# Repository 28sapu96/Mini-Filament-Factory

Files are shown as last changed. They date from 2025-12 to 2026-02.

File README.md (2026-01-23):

# Mini-Filament-Factory

-A DIY Machine to produce 1.75mm filament from plastic pellets

3D printing is cheap nowadays, with the average 1kg PLA spool costing $10-20. But, can we make it even cheaper? The answer is yes, and that is what this project aims to achieve. This is a machine that can take in cheap plastic pellets, with PLA pellets costing $2-3 per kg, and output usable 3D printer filament.  

# Project Goals
1. Filament should be acceptable by a 3D Printer, and it should print well
2. Should be easy to build and run
3. Filament should be cheap to make
4. Handles multiple types of plastic
5. Resistant to jamming and other mechanical flaws

# How Does This Work?

  To make 3D printer filament from plastic pellets, it first needs to be melted and extruded. This is the first phase. A Nema 17 stepper motor in the back drives a planetary gearbox with a 1:10 ratio. So, for every 10 rotations of the stepper motor, the output of the gearbox rotates once. Under ideal conditions, this increases the torque by 10 fold and decreases the speed by the same ratio, but in real life, friction and backlash, especially in 3D printed gears, causes energy losses which reduces the efficiency (power in vs power out). The output shaft of the gearbox then drives an auger 25mm in diameter and 430mm long (Although, the AliExpress listing doesn't tell us how long the twisty bit is, which means we can't buy a pipe of exact size). The auger rotates inside of a steel pipe which is also 25mm in inner diameter with some slight clearance. I considered using Aluminum for the pipe since it was cheaper, but the auger is made of HSS (High Speed Steel) which is much, much harder than Aluminum, so it will erode the Aluminum pipe and increase the gap between the auger and the pipe wall, which will create a gap for the molten plastic to flow back, which would be catastrophic. Steel also has a lot lower heat conductivity than aluminum, which might seem worse (since you need to heat up plastic), but it is better, since we don't want the heat from the end creeping up to the back where the hopper for plastic pellets is (it would make the plastic pellets stick early). Heat creep is also why there are fans between the end and the start of the pipe, to stop heat coming to the back of the pipe. The rotating auger pushes the pellets forward to the end of the pipe, where two 150W band heaters act as a hot end. The plastic exits through a nozzle (which is just a hole) that is ~1.75mm in diameter. The plastic then air cools, with fans assisting the process. 


  The filament doesn't come out with the diameter we need due to various factors such as die swell (molten plastic expands as it comes out of the hole), so we need to do some quality control. This is the second phase. The cooled filament strand goes into a diameter sensor. The filament passes through two roller bearings, one on the top and the other on the bottom. The one on the bottom is fixed, but the top one moves up and down with the filament diameter. The top bearing moves a lever arm, which amplifies the error by 7x. For example, if the filament is .1mm thicker than needed, the top bearing moves up .1mm, which moves the lever arm, which amplifies the distance, moving the neodymium magnet at the bottom by .7mm. The hall effect sensor picks up the motion of the magnet, and the arduino does some calculations to figure out the current filament diameter. 
  

  After the filament passes through the diameter sensor, it goes to the final phase, which is a puller. The puller also has two rollers, but only one is a bearing. The top one is a bearing that can be moved up or down by turning a small gear, which turns a larger gear with a 1:5 ratio, which turns a nut, which interfaces with a bolt at the top, moving it up or down. The bolt has a thread of 13 TPI (threads per inches), so for every 13 turns, the nut & bearing will move an inch. Spinning the small gear 5 times will turn the big gear 1 time. Spinning the big gear 1 time will move the nut by 1/13 inches, so spinning the small gear 1 time will move the nut by (1/13)/5 or 1/65 inches. The bottom roller is attached to a Nema 17 Pancake, which has just enough torque to pull the strand. The arduino controls the speed at which it pulls using the feedback from the diameter sensor. Faster pulling will thin out the filament, while slower pulling will thicken it. This process will ensure that we get accurate 1.75mm filament that can be accepted by a 3D printer.


# Full Wiring Diagram:

Mini Filament Factory

# CAD Images

Onshape Document: 
https://cad.onshape.com/documents/9f9f463344dcee8ce322f606/w/9856d2d31367ce1528b75580/e/936c6a3dbc2fb8e8e5b443f2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






# Bill of Materials
| Name | Description | Link | Quantity | Unit Price | Total Price | Running Total |
|---|---|---|---|---|---|---|
| LUJINXUN 30mmIDx50mmL\ | Band Heater | https://www.aliexpress.us/item/3256808522427468.html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 | 1 | $16.09 | $16.09 | $16.09 |
| 460mm x 25mm HSS Drill Bit | Auger Bit | https://www.aliexpress.com/item/3256809045870858.html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 | 1 | $13.29 | $13.29 | $29.38 |
| 304 Stainless Steel pipe 500mm 28ODx25ID | Steel Pipe | https://www.aliexpress.com/item/3256804686578512.html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 | 1 | $11.38 | $11.38 | $40.76 |
| MAX6675 | K Thermocouple + Amplifier  | https://www.aliexpress.com/ssr/300000512/BundleDeals2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 | 1 | $3.14 | $3.14 | $43.90 |
| Nema 17 Pancake | Stepper Motor | https://www.aliexpress.com/item/3256803688622110.html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 | 1 | $5.41 | $5.41 | $49.31 |
| 9025 12V Cooling Fan | Cooling Fan | https://www.aliexpress.com/item/3256806120222119.html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 | 4 | $3.82 | $15.28 | $64.59 |
| A4988 | Stepper Motor Driver | https://www.aliexpress.com/ssr/300000512/BundleDeals2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 | 2 | $2.71 | $5.42 | $70.01 |
| Refrigator Neodymium Magnets | 20x1mm Magnet | https://www.aliexpress.com/item/3256809781217883.html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 | 1 | $2.63 | $2.63 | $72.64 |
| SS49E | Hall Effect Sensor | https://www.aliexpress.com/item/3256808273062702.html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 | 1 | $1.59 | $1.59 | $74.23 |
| Deep Groove Ball Bearing | 15ODx6IDx5Wmm Bearing | https://jlcmc.com/product/b/C15/BR8364/deep-groove-ball-bearing-double-side-with-dust-cover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 | 4 | $0.12 | $0.47 | $74.70 |
| Deep Groove Ball Bearing Open Type | 28ODx15IDx7Wmm Bearing | https://jlcmc.com/product/b/C15/BR8362/deep-groove-ball-bearing-open-type?k=6902&productModelNumber=6902 | 4 | $0.26 | $1.06 | $75.75 |
| Hex Nut | 1/2""-13 | https://www.menards.com/main/hardware/fasteners-connectors/nuts/hex-jam-nuts/grip-fast-reg-hot-dipped-galvanized-grade-2-coarse-thread-hex-nuts/2325631/p-14444215289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 | 1 | $2.19 | $2.19 | $77.94 |
| Bolt | 1/2""-13 4-1/2"" | https://www.menards.com/main/hardware/fasteners-connectors/bolts/cap-screws-hex-bolts/grip-fast-reg-1-2-13-x-4-1-2-grade-2-galvanized-steel-hex-bolt-2-count/g2ls1241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 | 1 | $3.99 | $3.99 | $81.93 |
| Arduino Uno R3 | Microcontroller | https://www.aliexpress.us/item/3256806985353444.html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 | 1 | $5.12 | $5.12 | $87.05 |
| Solid State Relay | 3-32VDC - 24-380VAC 10A SSR | https://www.aliexpress.com/item/3256806596104544.html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 | 1 | $4.21 | $4.21 | $91.26 |
| Deep Groove Ball Bearing | 47ODx25IDx12Wmm Bearing | https://jlcmc.com/product/b/C15/BR8362/deep-groove-ball-bearing-open-type?k=6005&productModelNumber=6005 | 1 | $0.46 | $0.46 | $91.72 |
| Deep Groove Ball Bearing | 24ODx9IDx7Wmm Bearing | https://jlcmc.com/product/b/C15/BR8364/deep-groove-ball-bearing-double-side-with-dust-cover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 | 6 | $0.16 | $0.98 | $92.70 |
| Nema 17 | Stepper Motor | https://www.aliexpress.com/ssr/300000512/BundleDeals2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 | 1 | $5.72 | $5.72 | $98.42 |

# Building Instructions
-README, Firmware, guide continuation after assembly

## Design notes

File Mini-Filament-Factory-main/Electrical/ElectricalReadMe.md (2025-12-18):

Please follow the instructions for building the band heater circuit carefully. It deals with mains power from the outlet, which is enough to cause injury or death. Make sure to check according to the guide.

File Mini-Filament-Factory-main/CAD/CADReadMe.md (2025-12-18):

Some metal parts are excluded from the CAD assembly. Refer to the guide for better instructions. The ZIP folder contains all the individual parts, I recommend opening them up in a CAD software and then individually exporting them to print.

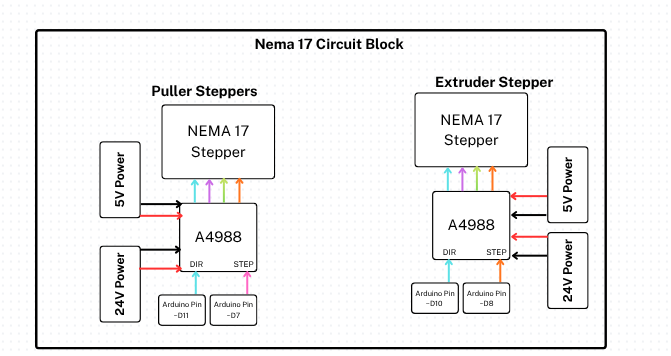
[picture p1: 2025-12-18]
Mini-Filament-Factory-main/Electrical/Stepper Circuit Block.png

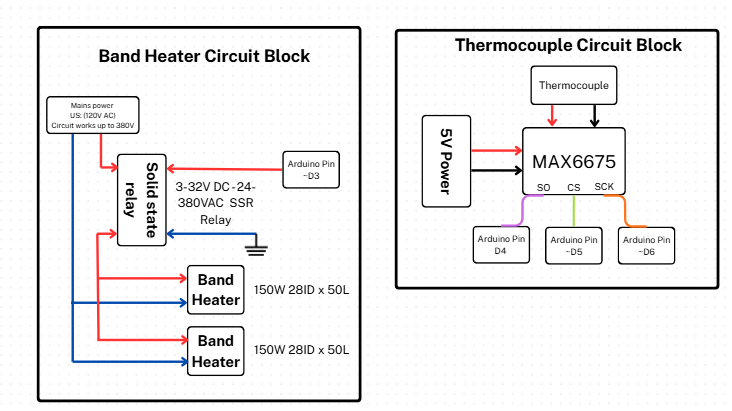
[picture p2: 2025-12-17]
Mini-Filament-Factory-main/Electrical/Circuit Diagram.png

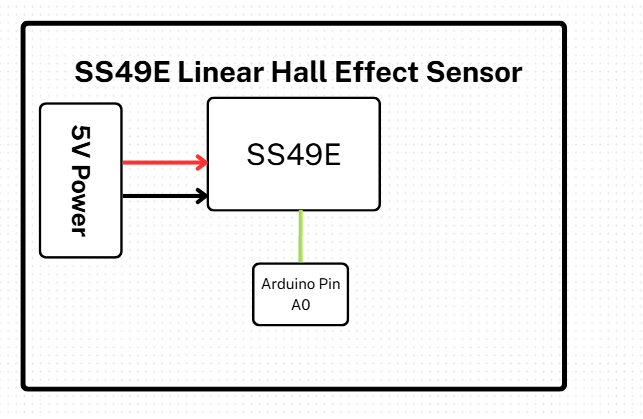
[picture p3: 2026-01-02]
Mini-Filament-Factory-main/Electrical/Screenshot 2026-01-02 100914.png

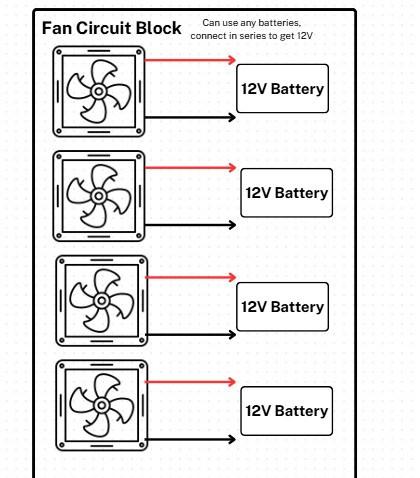
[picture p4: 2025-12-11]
Mini-Filament-Factory-main/Electrical/Circuit Block (2).png

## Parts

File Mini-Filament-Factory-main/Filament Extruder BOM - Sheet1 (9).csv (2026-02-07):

Name | Description | Link | Quantity | Unit Price | Total Price | Running Total
LUJINXUN 30mmIDx50mmL\ | Band Heater | https://www.aliexpress.us/item/3256808522427468.html?mp=1 | 1 | $16.09 | $16.09 | $16.09
460mm x 25.4mm HSS Drill Bit | Auger Bit | https://www.aliexpress.com/item/3256809045870858.html?mp=1 | 1 | $13.29 | $13.29 | $29.38
Mild Steel Tubing - 1 1/4" O.D. - .120" wall | Steel Pipe (Make sure to put 2 as the cut length, price per foot) | https://www.appliedracing.com/tubing-and-plate/4130-chromoly---erw-mild-steel---dom-tubing/33---mild-steel-tubing---1-1-4-od---120-wall.html | 2 | $4.25 | $8.50 | $37.88
MAX6675 | K Thermocouple + Amplifier | https://www.aliexpress.com/ssr/300000512/BundleDeals2?productIds=1005005272656611:12000032439762794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 | 1 | $3.19 | $3.19 | $41.07
Nema 17 Pancake | Stepper Motor | https://www.aliexpress.com/item/3256803688622110.html?mp=1 | 1 | $5.41 | $5.41 | $46.48
9025 12V Cooling Fan | Cooling Fan | https://www.aliexpress.com/item/3256806120222119.html?mp=1 | 4 | $3.82 | $15.28 | $61.76
A4988 | Stepper Motor Driver | https://www.aliexpress.com/ssr/300000512/BundleDeals2?productIds=1005005281739306:12000040072246972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 | 2 | $2.03 | $4.06 | $65.82
Refrigator Neodymium Magnets | 20x1mm Magnet | https://www.aliexpress.com/item/3256809781217883.html?mp=1 | 1 | $2.63 | $2.63 | $68.45
SS49E | Hall Effect Sensor | https://www.aliexpress.com/item/3256808273062702.html?mp=1 | 1 | $1.59 | $1.59 | $70.04
Deep Groove Ball Bearing | 15ODx6IDx5Wmm Bearing | https://jlcmc.com/product/b/C15/BR8364/deep-groove-ball-bearing-double-side-with-dust-cover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 | 4 | $0.12 | $0.47 | $70.51
Hex Nut | 1/2"-13 | https://www.menards.com/main/hardware/fasteners-connectors/nuts/hex-jam-nuts/grip-fast-reg-hot-dipped-galvanized-grade-2-coarse-thread-hex-nuts/2325631/p-1444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 | 1 | $2.19 | $2.19 | $72.70
Bolt | 1/2"-13 4-1/2" | https://www.menards.com/main/hardware/fasteners-connectors/bolts/cap-screws-hex-bolts/grip-fast-reg-1-2-13-x-4-1-2-grade-2-galvanized-steel-hex-bolt-2-count/g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 | 1 | $3.99 | $3.99 | $76.69
Arduino Uno R3 | Microcontroller | https://www.aliexpress.us/item/3256806985353444.html?curPageLogUid=Nm4N0lD3CbWR | 1 | $5.12 | $5.12 | $81.81
Solid State Relay | 3-32VDC - 24-380VAC 10A SSR | https://www.aliexpress.com/item/3256806596104544.html?mp=1 | 1 | $4.21 | $4.21 | $86.02
Nema 17 | Stepper Motor | https://www.aliexpress.com/ssr/300000512/BundleDeals2?productIds=1005005281739306:12000040072246972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 | 1 | $5.72 | $5.72 | $91.74
Ball Bearing 608 | Ball Bearing | https://jlcmc.com/product/b/C15/BR8362/deep-groove-ball-bearing-open-type | 8 | $0.11 | $0.90 | $92.63
Brass Nozzle | 2mm M6 | https://www.aliexpress.us/item/3256808717405097.html?mp=1 | 1 | $3.54 | $3.54 | $96.17

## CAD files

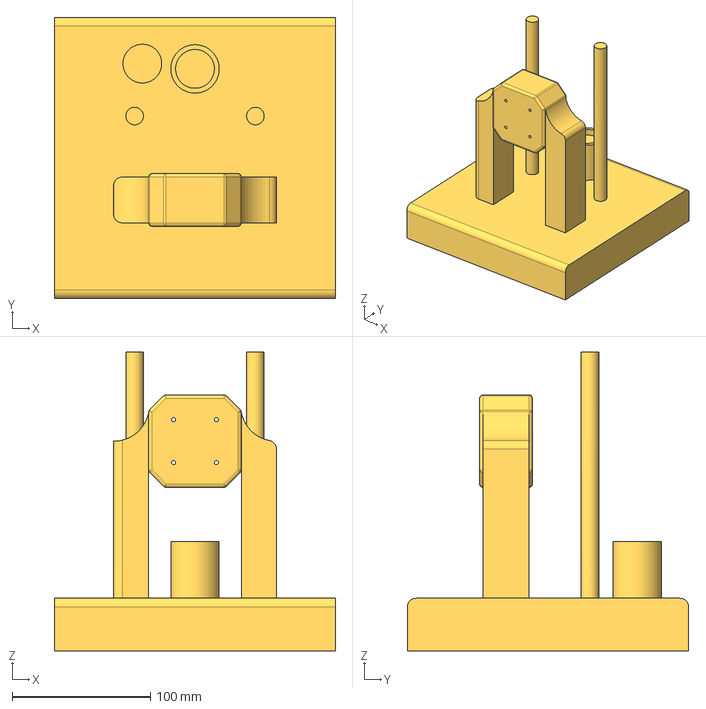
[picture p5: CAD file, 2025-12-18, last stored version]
Mini-Filament-Factory-main/CAD/Machine Assembly W- Nema 23 driver - Part 9.step
203.2 x 203.2 x 215.9 mm

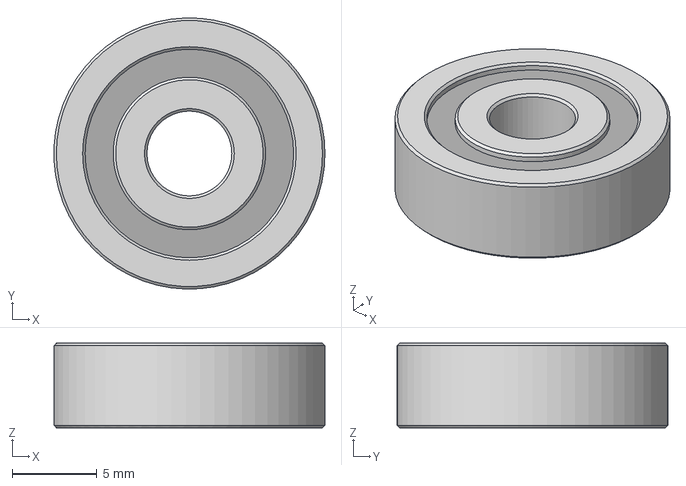
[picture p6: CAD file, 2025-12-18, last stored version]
Mini-Filament-Factory-main/CAD/Machine Assembly W- Nema 23 driver - 625ZZ_1.step
16.0 x 16.0 x 5.00 mm

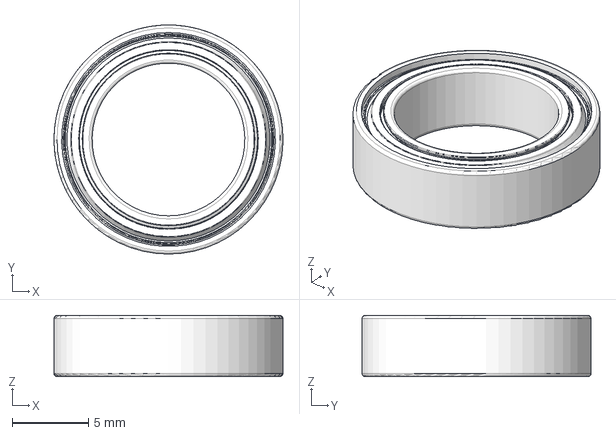
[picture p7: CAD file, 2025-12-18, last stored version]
Mini-Filament-Factory-main/CAD/Machine Assembly W- Nema 23 driver - 1765304562009.step
15.0 x 15.0 x 4.00 mm

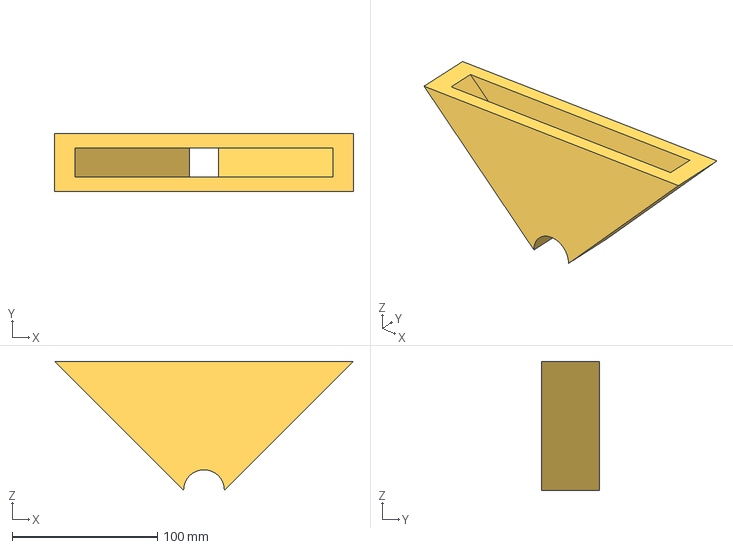
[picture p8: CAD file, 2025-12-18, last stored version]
Mini-Filament-Factory-main/CAD/Machine Assembly W- Nema 23 driver - Part 7.step
206.1 x 40.0 x 89.0 mm

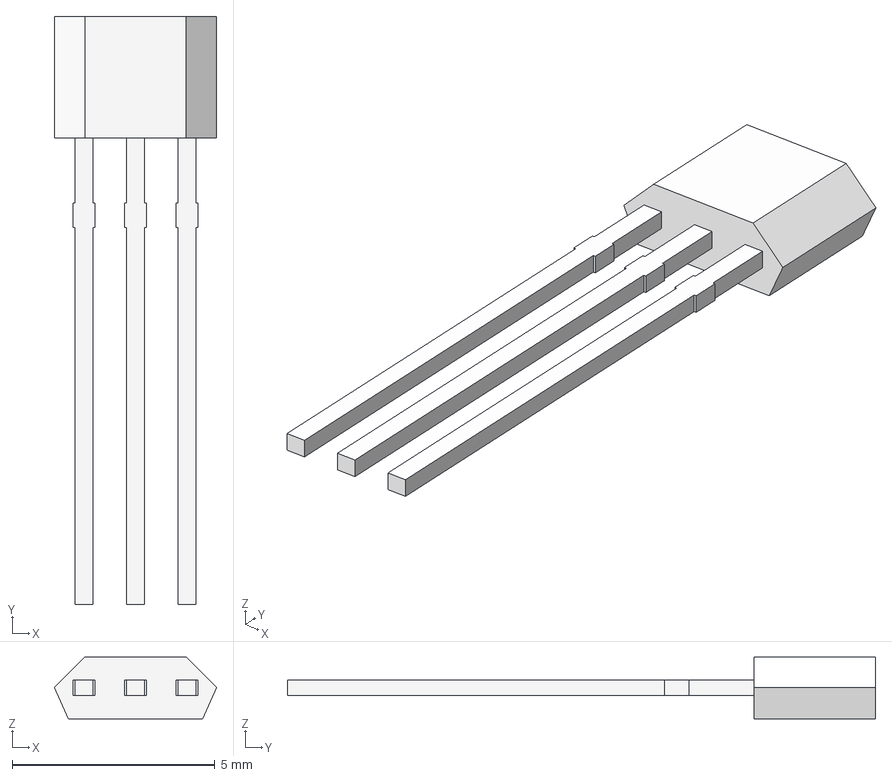
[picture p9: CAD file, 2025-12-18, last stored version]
Mini-Filament-Factory-main/CAD/Machine Assembly W- Nema 23 driver - SS49E Linear Hall Effect.step
4.00 x 14.5 x 1.52 mm

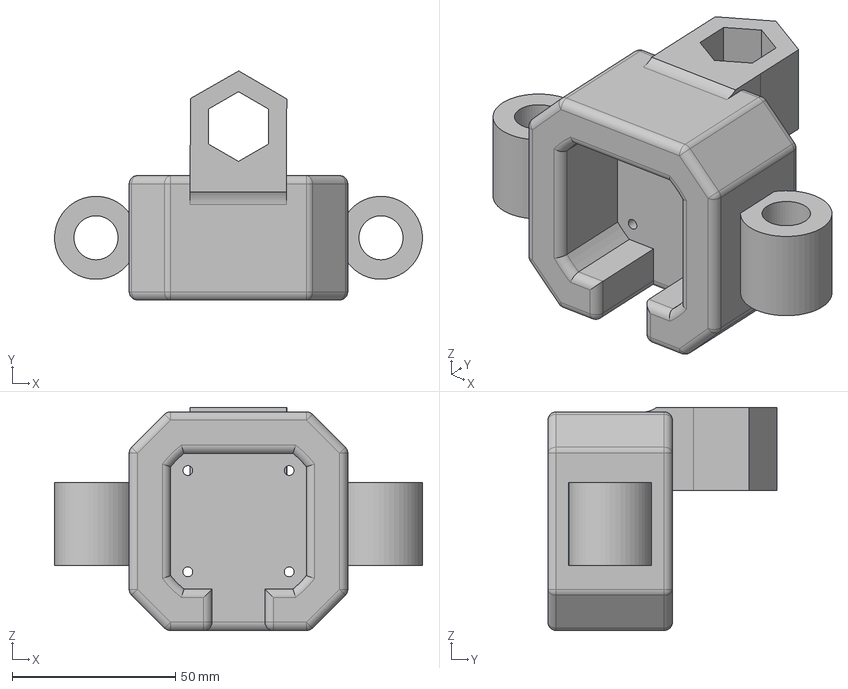
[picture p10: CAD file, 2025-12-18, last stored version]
Mini-Filament-Factory-main/CAD/Machine Assembly W- Nema 23 driver - Part 5.step
112.6 x 70.1 x 68.2 mm

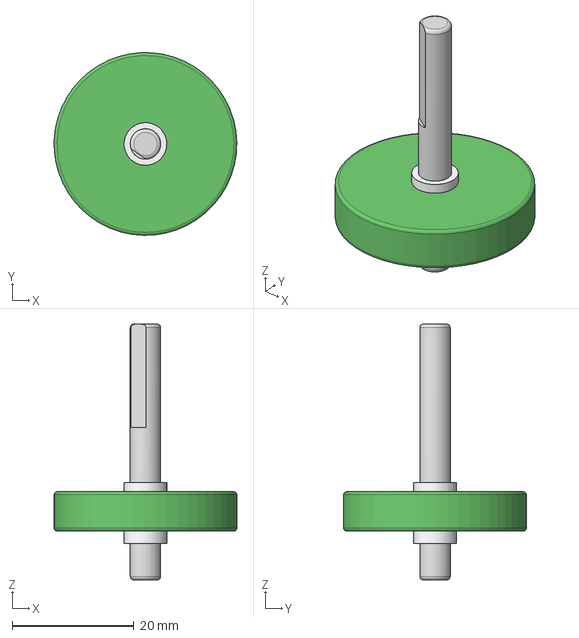
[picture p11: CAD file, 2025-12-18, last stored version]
Mini-Filament-Factory-main/CAD/Machine Assembly W- Nema 23 driver - rotor.step
30.0 x 30.0 x 42.0 mm

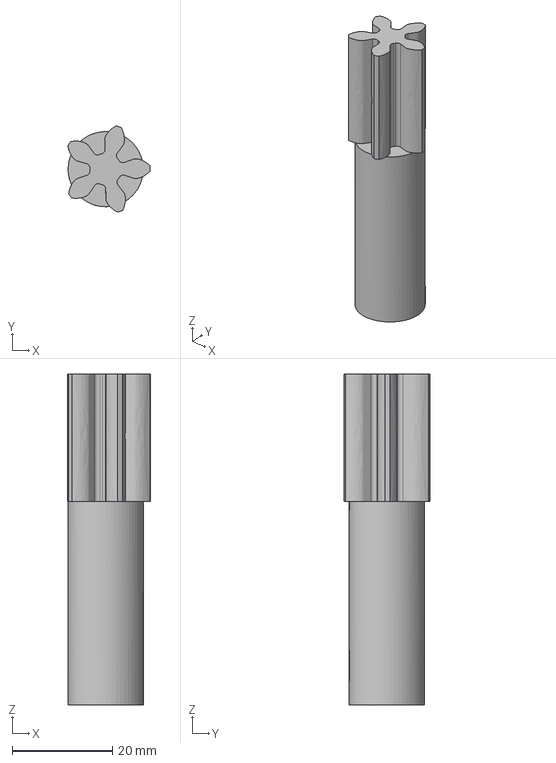
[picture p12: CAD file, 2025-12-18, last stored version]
Mini-Filament-Factory-main/CAD/Machine Assembly W- Nema 23 driver - Part 8.step
16.5 x 17.2 x 66.0 mm

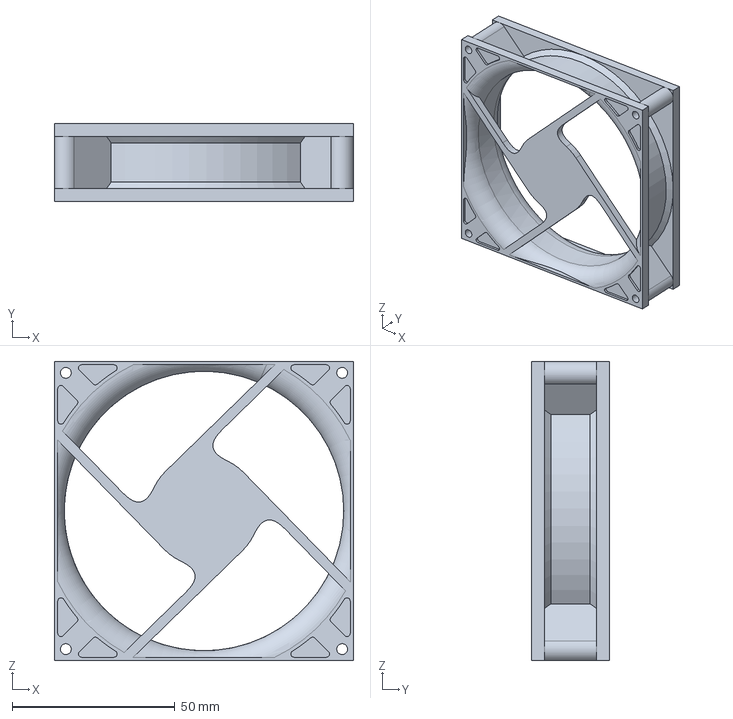
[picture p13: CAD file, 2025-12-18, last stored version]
Mini-Filament-Factory-main/CAD/Machine Assembly W- Nema 23 driver - computer system fan v3.step
92.0 x 24.0 x 92.0 mm

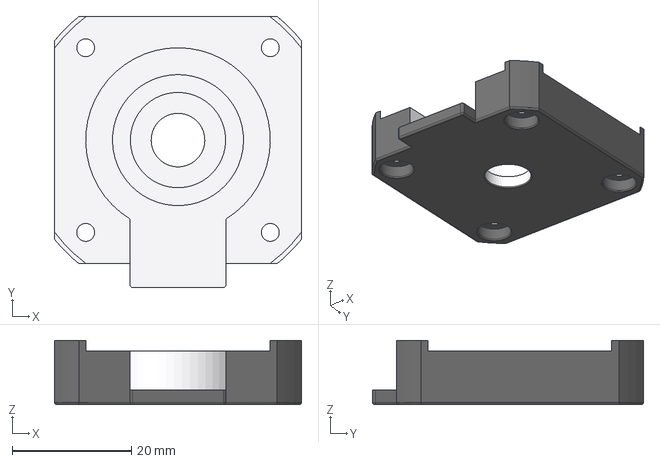
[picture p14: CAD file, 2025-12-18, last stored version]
Mini-Filament-Factory-main/CAD/Machine Assembly W- Nema 23 driver - back_plate.step
41.5 x 45.5 x 10.8 mm

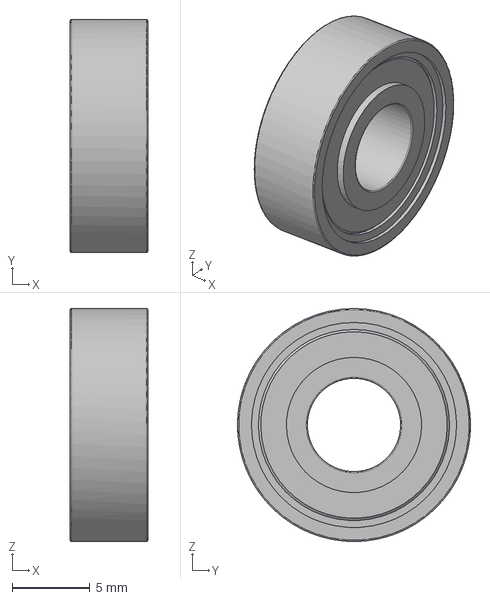
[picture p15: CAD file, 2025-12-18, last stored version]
Mini-Filament-Factory-main/CAD/Machine Assembly W- Nema 23 driver - 1764810303908.step
5.00 x 15.0 x 15.0 mm

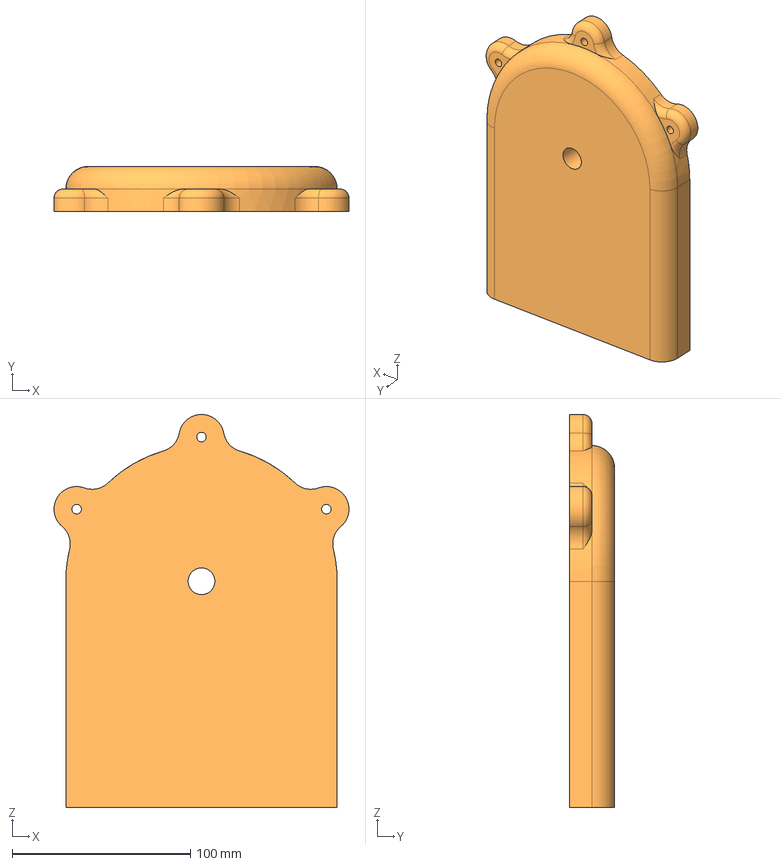
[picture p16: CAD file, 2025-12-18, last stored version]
Mini-Filament-Factory-main/CAD/Machine Assembly W- Nema 23 driver - Part 15.step
165.6 x 25.4 x 220.6 mm

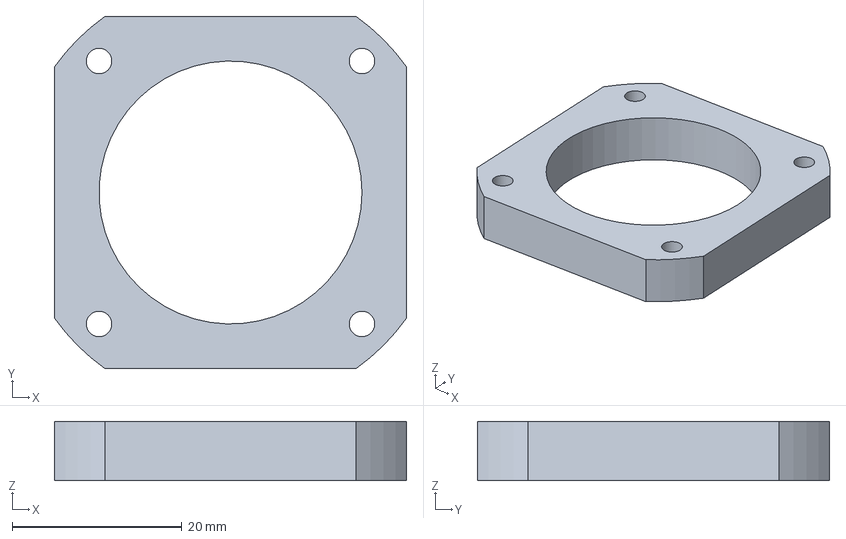
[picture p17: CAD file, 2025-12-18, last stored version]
Mini-Filament-Factory-main/CAD/Machine Assembly W- Nema 23 driver - stator.step
41.5 x 41.5 x 7.00 mm

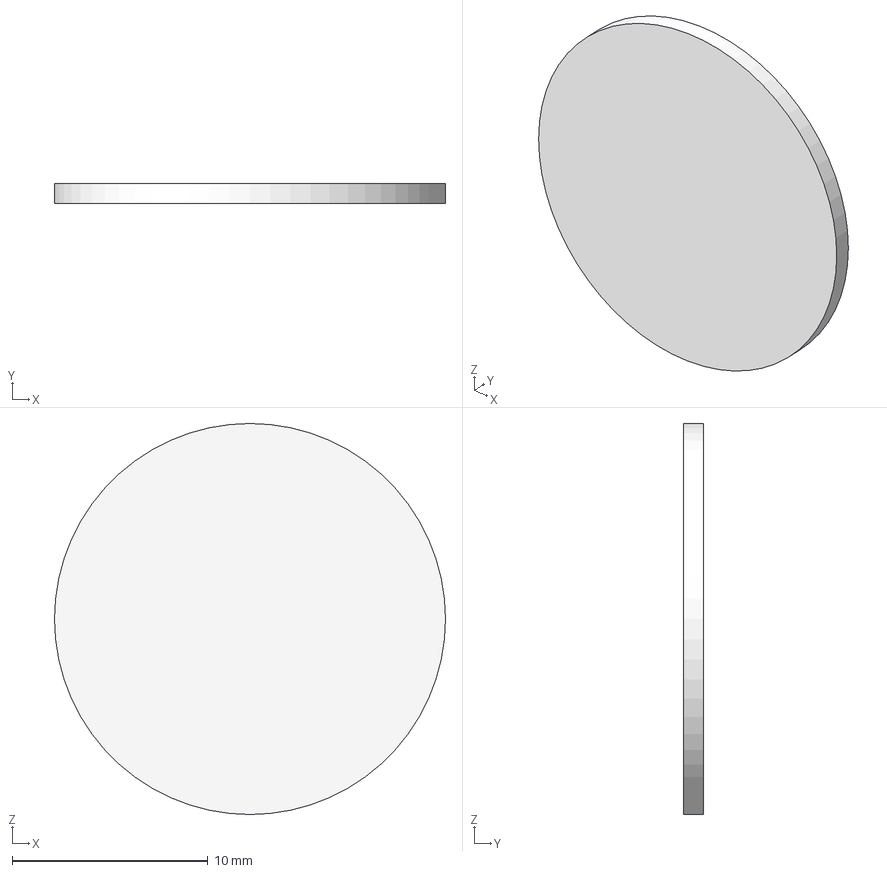
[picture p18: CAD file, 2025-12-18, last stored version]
Mini-Filament-Factory-main/CAD/Machine Assembly W- Nema 23 driver - Part 4.step
20.0 x 1.00 x 20.0 mm

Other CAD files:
Mini-Filament-Factory-main/CAD/Machine Assembly W- Nema 23 driver - 625ZZ.step
Mini-Filament-Factory-main/CAD/Machine Assembly W- Nema 23 driver - Part 3.step
Mini-Filament-Factory-main/CAD/Machine Assembly W- Nema 23 driver - Part 1.step
Mini-Filament-Factory-main/CAD/Machine Assembly W- Nema 23 driver - front_plate.step
Mini-Filament-Factory-main/CAD/Machine Assembly W- Nema 23 driver - 1764810303908 (1).step
Mini-Filament-Factory-main/CAD/Machine Assembly W- Nema 23 driver - 1764810303908 (2).step
Mini-Filament-Factory-main/CAD/Machine Assembly W- Nema 23 driver - 1765301354431.step
Mini-Filament-Factory-main/CAD/Machine Assembly W- Nema 23 driver - 1765301366085.step
Mini-Filament-Factory-main/CAD/Machine Assembly W- Nema 23 driver - M3_screw.step
Mini-Filament-Factory-main/CAD/Machine Assembly W- Nema 23 driver - M3_screw_1.step
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

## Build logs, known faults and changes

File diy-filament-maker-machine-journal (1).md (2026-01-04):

<!--
  This journal is auto generated by Hack Club Blueprint.
-->

## 12/3/2025 - Preliminary Concept  

_Time spent: 1.5h_  

I looked at industrial and DIY filament machine designs to find some ideas/inspiration. Eventually, I came up with a simple working diagram for the machine. I plan on laying the machine out in a line, like an assembly line. Now that I have the concept laid down, the next thing is to fire up CAD (onshape) and start making an actual design.image (1)

## 12/4/2025 - Created Motor Mount & Gearbox  

_Time spent: 4.0h_  

In the last journal, I created a preliminary concept that showed how the machine would function. The screw conveyer will be an auger screw that will be driven by a drive mechanism. So today, I made the drive mechanism. I had a 4200W 4092 1050kv Hobbystar motor lying around at home, so I decided to base my design off of that. I researched planetary gears, and after a few hiccups I was able to create a perfectly meshing planetary gearbox. It has a gear ratio of 3125:1 and is in the planetary arrangement (Stationary ring). To drive the motor, I will be using a Sequre 28120 AM32 ESC running at 32V. The motor RPM will be 33600(kV * V => 1050*32) when it is running at max voltage. The gearbox will output around 10.7RPM (RPM/Gear Ratio => 33600/3125) which should be enough to drive the screw conveyer.





## 12/6/2025 - Redesigned the Planetary Gearbox  

_Time spent: 2.0h_  

In the last journal entry, I created a motor mount and planetary gearbox. I was just looking over the design, and I noticed that the dimensions of the gears in the gearbox aren't thick enough to support the loads that it needs to. So, I went in and deleted the old 3125:1 gearbox and created a new design. This time, I made sure to make the gears thick enough to handle the loads. I also reduced the gear ratio down to 10:10:10, or 1:1000. This way, the output will have a higher RPM range, being from 0 to 33.6. The cad design and assembly both took an hour, which is less than the time it took for the first gearbox (this time I had some experience from making the old design). 


## 12/8/2025 - Finished Filament Diameter Sensor  

_Time spent: 3.0h_  

To get usable filament, we need to make sure that the filament is accurate to +-0.1mm in diameter. To achieve this, we need something that senses the diameter of the filament and sends commands to the puller mechanism ahead. If the diameter is too small, the puller will pull slower, and vice versa. The filament goes through the middle two bearings on the top. The gap between the two bearings is the wanted diameter, 1.75mm. The top bearing is connected to a lever arm, with its fulcrum (rotation point) being another bearing. The lever arm has an amplification ratio of ~4.8. This means that if the filament diameter changes by .1mm, the magnet at the bottom will move by .48mm. The magnet at the bottom interacts with a SS94E hall effect sensor, which senses the changes in magnetic field. As the magnet moves, the hall effect sensor will pick that up and send it to the Arduino, which will do calculations to adjust the puller speed as needed. 



## 12/9/2025 2 PM - Finished Puller Mechanism  

_Time spent: 3.0h_  

The filament comes out of the nozzle bigger or smaller than the desired diameter. To solve this problem, a pulling mechanism needs to be used that pulls the filament based on the filament diameter. This mechanism uses 2 wheels that are driven by nema17 stepper motors. Using stepper motors allows precise control over the speed of the rollers. The bottom stepper motor is fixed to the base, while the top one can move up and down. A nut is attached to the top stepper motor, which is attached to a rotatable bolt. The bolt is connected to a reduction gear so it can be moved in very small increments. 

## 12/9/2025 10 PM - Created Fan Mount, Extruder, & Finalized Design  

_Time spent: 4.0h_  

I made the final two pieces of the puzzle: the extruder and fan mount. The extruder has a hopper in the back that takes in plastic pellets. The stainless-steel pipe has a rectangular opening of 20x20mm. The pipe and the auger have an inside diameter of 25mm. The pipe will have to be slightly shaved down by ~.3-.4mm to allow the auger to rotate but also prevent backflow (the molten plastic shouldn't flow back through the gap between the auger and pipe). At the end, there is a cap with a 2mm hole, which is where the filament comes out of. The auger is coupled to the gearbox in the back using a hex coupling. There are 4 90x25mm fans that blow at different parts of the assembly. The first one blows at the joint between the auger shaft and the PLA gearbox output shaft, so that the 3D printed part doesn't soften due to heat. The 2nd fan blows between the cold and hot sections of the barrel, so that the plastic pellets can enter the screw conveyer and travel to the end without sticking. The last 100mm section of the pipe has two 150W 30x50mm band heaters which can heat up to 400*C. The last 2 fans blow at the filament exiting the nozzle to cool and harden the outer layer. The entire assembly will be screwed into a base piece of wood. The next and final step before getting to building hands on will be creating the electrical systems.  





## 12/10/2025 8 PM - Changed Drive Mechanism  

_Time spent: 2.0h_  

The planetary gearbox and the 4200W motor I was using earlier was super overkill for what it was meant for, and it was very expensive. So, I switched over to using a Nema 23 stepper motor with a TB6600 driver, which is a lot more accurate, is a lot cheaper, and is also meant for this purpose. Choosing the motor and driver took most of the time, as designing the mount for it in CAD was easy. 



## 12/10/2025 10 PM - Finalized electrical systems and machine assembly  

_Time spent: 3.0h_  

I spent some time completing the basic wiring diagram for the machine and finalized the assembly in Onshape. The electrical systems will be powered by the wall outlet and a bench power supply. After I did that, I went over the BOM and made sure everything was there and got the project ready for the 1st review.Circuit Block (2)
Circuit Block (3)Circuit Block (1)

## 12/17/2025 - Reduced motor sizes on extruder & minor changes to puller  

_Time spent: 1.5h_  

To save costs, I downsized the extruder motor from a NEMA 23 to a NEMA 17. A Nema 17 on its own won't supply the torque needed to turn the 25MM auger and overcome the pressure required to push the plastic forward, so I will pair it with a 10:1 planetary gearbox that is beefy enough to handle axial loads. The puller motors still use the same Nema 17 Pancake motor (smaller version of a NEMA 17 - used in 3D printer extruders), but only 1 instead of 2. The 2nd roller is now an idler bearing. The idler bearing can move up and down by rotating the small gear, which turns the big gear at a 5:1 ratio, which turns a bolt. The bolt has 13 threads per inch, so a full rotation of the small gear will move the idler bearing .4mm up or down. I could use Nema 14 motors for the puller, but I couldn't find any on AliExpress that are cheaper than my Nema 17s, and they would bring up other issues, so I just stuck with the old configuration. Any motor smaller than a Nema 14 won't supply enough torque to pull the filament strand through the machine, and it won't run for long without overheating or slipping (e.g., a 28BYJ-48 stepper motor). Reliability will drop with smaller motors, and reliability is super important for making a consistent 1.75mm filament. The circular-to-hex coupling (gearbox to auger) will probably be 3D printed, or I will find another solution to it. The hex dimensions aren't specified in the seller's listing, and a hex-to-circular coupling with the appropriate dimensions is rare. Therefore, 3D printing it will likely be the best option.




## 1/2/2026 - Added Info to ReadMe and Created Base Firmware  

_Time spent: 3.0h_  

I updated the ReadMe with wiring diagrams and an explanation of the machine. I created some basic code for the entire machine. The code uses PID modulation twice to control temperature of the band heater and puller speed to control the filament diameter. 



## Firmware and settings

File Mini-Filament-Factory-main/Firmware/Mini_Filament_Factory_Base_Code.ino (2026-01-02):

#include <MAX6675.h>
#include <AccelStepper.h>
#include <PID_v1.h>

// --- PIN DEFINITIONS
#define THERMO_SO  4
#define THERMO_CS  5
#define THERMO_SCK 6
#define SSR_PIN    3
#define HALL_PIN   A0
#define PULL_STEP  7
#define PULL_DIR   11
#define EXT_STEP   8
#define EXT_DIR    10

// --- PID TEMPERATURE CONTROL
double targetTemp = 270.0;
double currentTemp, tempOutput;
double Kp_T = 50, Ki_T = 1.5, Kd_T = 20; // PID Constants
PID tempPID(&currentTemp, &tempOutput, &targetTemp, Kp_T, Ki_T, Kd_T, DIRECT);

// --- PID DIAMETER CONTROL (PULLER)
double targetDia = 1.75;
double currentDia, pullerSpeed; // pullerSpeed is the PID Output
double Kp_D = 150, Ki_D = 10, Kd_D = 5; // PID Constants
PID pullerPID(&currentDia, &pullerSpeed, &targetDia, Kp_D, Ki_D, Kd_D, DIRECT);

// --- HARDWARE
MAX6675 thermocouple(THERMO_SCK, THERMO_CS, THERMO_SO);
AccelStepper extruder(AccelStepper::DRIVER, EXT_STEP, EXT_DIR);
AccelStepper puller(AccelStepper::DRIVER, PULL_STEP, PULL_DIR);

unsigned long windowSize = 1000;
unsigned long windowStartTime;

void setup() {
  Serial.begin(115200);
  windowStartTime = millis();

  // PID 1 Config (Heater)
  tempPID.SetOutputLimits(0, windowSize);
  tempPID.SetMode(AUTOMATIC);

  // PID 2 Config (Puller)
  pullerPID.SetOutputLimits(100, 1000); 
  pullerPID.SetMode(AUTOMATIC);

  extruder.setMaxSpeed(2000);
  puller.setMaxSpeed(2000);
  pinMode(SSR_PIN, OUTPUT);
}

void loop() {
  // INPUT SENSING
  currentTemp = thermocouple.getCelsius();
  
  // Hall Effect Mapping 
  int rawHall = analogRead(HALL_PIN);
  // Calibration: Replace 450 and 550 with measured min max with objects of 1.5mm and 2mm dia respectively
  currentDia = map(rawHall, 450, 550, 150, 200) / 100.0;

  // PID CALCULATIONS
  tempPID.Compute();
  
  if (currentTemp >= 240.0) // Only run puller PID if plastic is molten
  {
    pullerPID.Compute();
  }

  //HEATER OUTPUT
  unsigned long now = millis();
  if (now - windowStartTime > windowSize) windowStartTime += windowSize;
  digitalWrite(SSR_PIN, tempOutput > (now - windowStartTime) ? HIGH : LOW);

  // STEPPER OUTPUT
  if (currentTemp >= 240.0) {
    extruder.setSpeed(250); // Master speed (Constant)
    puller.setSpeed(pullerSpeed); // Slave speed (Variable via PID)
    
    extruder.runSpeed();
    puller.runSpeed();
  } else {
    extruder.stop();
    puller.stop();
  }

  // 5. DEBUGGING
  static unsigned long lastUpdate = 0;
  if (millis() - lastUpdate > 500) {
    Serial.print("T:"); Serial.print(currentTemp);
    Serial.print(" D:"); Serial.print(currentDia);
    Serial.print(" vPull:"); Serial.println(pullerSpeed);
    lastUpdate = millis();
  }
}

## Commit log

2025-12-08 Enhance README with project introduction
    Added a brief introduction about the cost-effectiveness of producing filament from plastic pellets.
2025-12-10 All the CAD parts in the final assembly
    Note: All the parts listed in the BOM may not be present in the final assembly. Refer to the building guide for the most accurate assembly. I will probably make an assembly video for this project.
2025-12-11 Delete Machine ASsembly.zip
    Old Assembly
2025-12-11 Final Assembly (All CAD Parts)
    This is all the parts used in the final assembly of the machine. Although, beware, there are some additional parts that are used in real life. Refer to the building guide/process for more information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
2025-12-11 Delete Filament Extruder BOM - Sheet1.csv
    Old BOM
    [Filament Extruder BOM - Sheet1.csv]
2025-12-11 Updated BOM
    [Filament Extruder BOM - Sheet1 (2).csv]
2025-12-18 Create CADReadMe.md for assembly parts information
    Added a readme file for CAD parts used in assembly.
2025-12-18 Add disclaimer about excluded metal parts in CAD
2025-12-18 Update CADReadMe with additional printing instructions
    Added recommendation to open parts in CAD software and export for printing.
2025-12-18 Create ElectricalReadMe.md with safety guidelines
    Added safety instructions for building the band heater circuit.
2025-12-18 Stepper Circuit Block
2025-12-18 Rename Stepper Circuit Block to Stepper Circuit Block.png
2025-12-31 Updated Link
    [Filament Extruder BOM - Sheet1 (6).csv]
2025-12-31 Updated Links
    [Filament Extruder BOM - Sheet1 (6).csv]
2025-12-31 Enhance filament production process description in README
    Added detailed explanation of the filament production process, including phases of melting, extrusion, quality control, and pulling mechanisms.
2026-01-02 Hall Effect
2026-01-02 Update README with wiring diagram and CAD links
    Added wiring diagram and CAD images links to README.
2026-01-14 Add more images to CAD Images section
    Added additional images to the CAD Images section of the README.
2026-01-14 Expand README with filament production details
    Added detailed explanations of the 3D printing filament production process, including the melting, extrusion, quality control, and pulling phases.
2026-01-23 Add Bill of Materials section to README
    Added a Bill of Materials section with detailed item listings, including descriptions, links, quantities, unit prices, and total prices.
